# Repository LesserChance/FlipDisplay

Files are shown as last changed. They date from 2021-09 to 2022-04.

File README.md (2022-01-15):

# Flip Display

https://user-images.githubusercontent.com/819400/149609962-681a9211-6ebb-46da-95a2-772721c91d99.mp4

This is a 3D-printed flip character display. Each character utilizes a position sensor for loop detection in order to ensure accuract positioning of character display. The display is capable of a few different animation styles, e.g. all arriving at the same time, or cascading left-to-right. It has a simple web-based UI and API, and is fairly easy to construct.

## UI
The ESP32 hosts a web server that serves a simple web page and API that allows you to update the display.

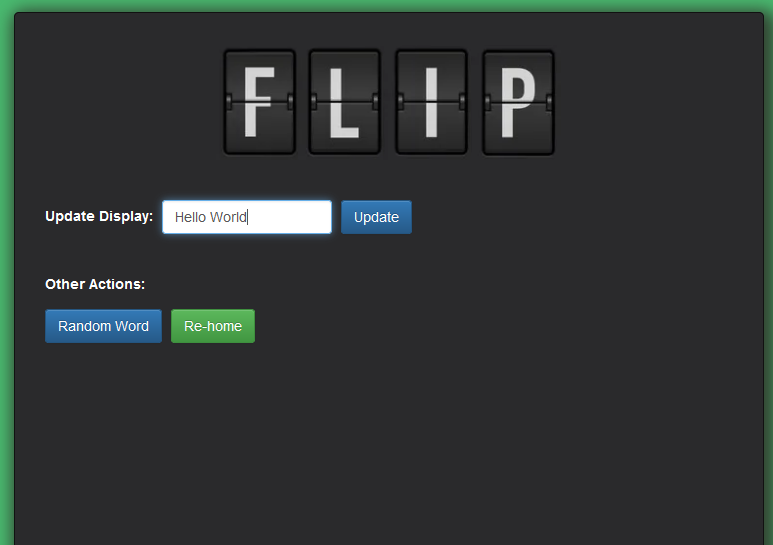
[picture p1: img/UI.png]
UI


## Electronics
There are only a few different major components: A buck convertor, an ESP32, and an A4988 Motor driver (per character)

### PCB: Main
The main panel is used as the power bus and ESP32 break out. It connects each motor step pin and loop detection button pin to an individual GPIO pin, and connects all driver enable pins to a single GPIO pin. There is also a section for screw terminals for easy access to all ESP32 pins, as well as power.

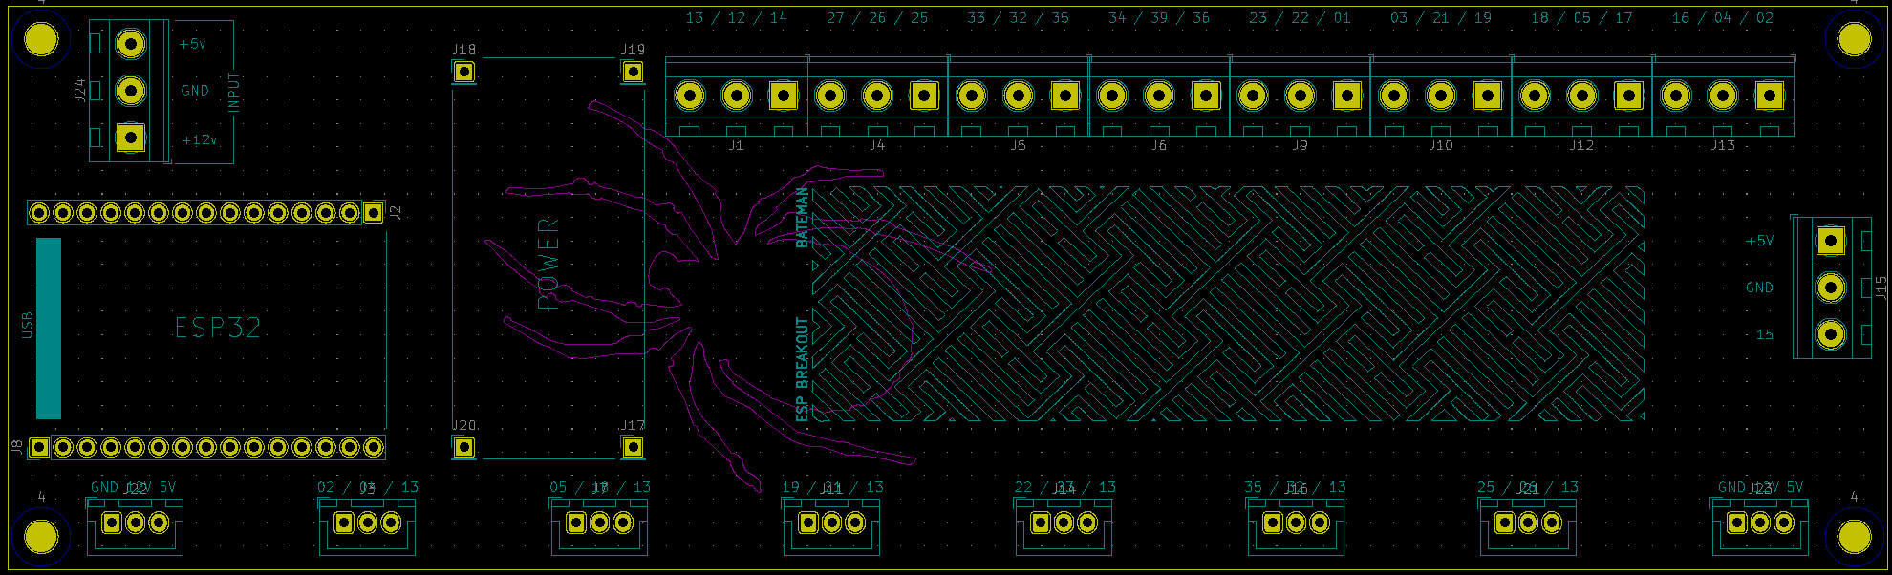
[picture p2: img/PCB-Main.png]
Main PCB


### PCB: Motor
One motor panel exists per character. This acts as the interface between the A4988 Motor Driver, the motor, and the ESP32.

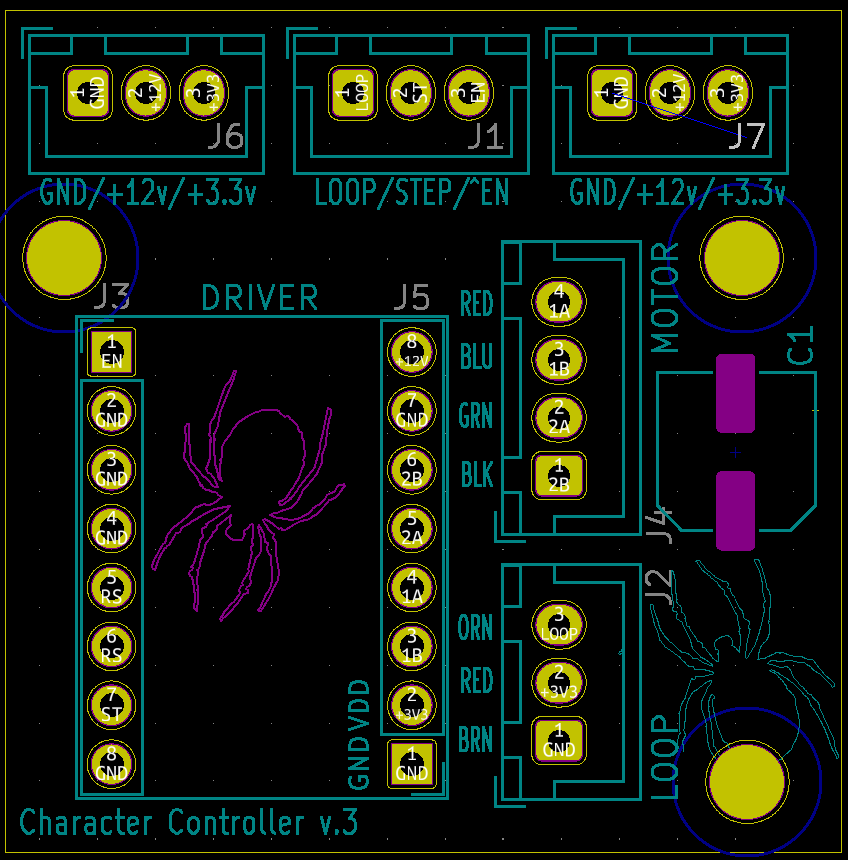
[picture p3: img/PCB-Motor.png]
Motor PCB


## Models
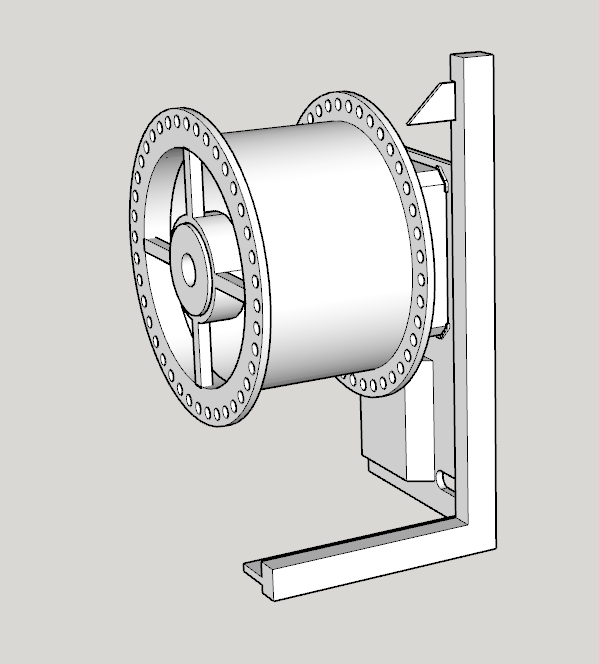
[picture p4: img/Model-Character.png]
models


The character models are designed to be nested against one another and to minimize the distance between characters as much as possible.

### Assembly 1: The Barrel
The barrel and the stator connect to one another, and the flaps are placed within the holes.

### Assembly 2: The Bracket
A motor is mounted to the bracket. The button holder is connected to the two front bottom holes on the motor and a leaf switch button is glued on. The barrel assembly is connected to the motor with a coupler so that it rotates around the motor housing. A stopper is fastened into the top of the bracket, which is used to stop the letters at a certain position

### Assembly 3: Circuit
The circuit assembly is just used to house the individual PCBs.

---

Originally inspired from designs by [hakernia on Thingiverse](https://www.thingiverse.com/thing:2369832), but I found that the small motor was not driving well, as it'd get hot and fail, or get stuck easily. So I upgraded to heavier duty Nema17 Motorslike the ones used in 3D Printers and decided to use an actual coupler to connect the 3d printed parts to the motor.

## Supplies and Costs
A 6 character Flip Display will cost about $170.00 USD for all the raw materials, then additional costs based on your enclosure.  

Filament: $40.00 USD  
Electronics: $100.00 USD  
PCBs: $30.00 USD  

### Bill of Materials
All models were printed using [MatterHackers Build Series PLA](https://www.matterhackers.com/store/l/175mm-pla-filament-black-1-kg/sk/MY6CYEZM) on a Creality 10s Pro V2.
| Part | Supply | Cost | Count |
|---|---|---|---|
|Black PLA|[MatterHackers](https://www.matterhackers.com/store/l/175mm-pla-filament-black-1-kg/sk/MY6CYEZM)|$19.00|1|
|White PLA|[MatterHackers](https://www.matterhackers.com/store/l/175mm-pla-filament-white-1-kg/sk/MEEDKTKU)|$19.00|1|

Electronics and hardware were sourced through a few different providers.

| Component | Part | Supply | Cost | Count |
|---|---|---|---|---|
|-|12v Power adaptor|[Amazon](https://www.amazon.com/gp/product/B07FFKL7CR/ref=ppx_yo_dt_b_asin_title_o05_s00)|$19.00|1|
|Main|Buck Convertor|[Amazon](https://www.amazon.com/gp/product/B07QKHR6PY/ref=ppx_yo_dt_b_asin_title_o05_s00)|$1.50|1|
|Main|ESP32|[Amazon](https://www.amazon.com/gp/product/B08246MCL5/ref=ppx_yo_dt_b_asin_title_o04_s00)|$7.00|1|
|Main|Panel Mount Micro USB Extension|[Amazon](https://www.amazon.com/gp/product/B082HZKVP1/ref=ppx_yo_dt_b_asin_title_o05_s01)|$11.00|1 (optional)|
|Main|15 Pin Header|[Tayda](https://www.taydaelectronics.com/15-pin-2-54-mm-single-row-female-pin-header.html)|$0.12|2|
|Main|Screw Terminal|[Tayda](https://www.taydaelectronics.com/dg300-screw-terminal-block-3-positions-5mm.html)|$0.14|A bunch|
|Motor|Nema17 Stepper Motor|[Amazon](https://www.amazon.com/gp/product/B07THK8RS1/ref=ppx_yo_dt_b_asin_title_o01_s00)|$7.40|1 per character|
|Motor|A4988 Motor Driver|[Amazon](https://www.amazon.com/gp/product/B092PZNFNS/ref=ppx_yo_dt_b_asin_title_o05_s00)|$1.40|1 per character|
|Motor|Coupler|[Amazon](https://www.amazon.com/gp/product/B0852P8WSH/ref=ppx_yo_dt_b_asin_title_o09_s00)|$0.90|1 per character|
|Motor|10mm x 26mm x8mm Bearing|[Digikey](https://www.digikey.com/en/products/detail/mechatronics-bearing-group/6000-2RS/9608370)|$0.85|1 per character|
|Motor|Leaf Switch|[Mouser](https://www.mouser.com/ProductDetail/612-MS0850506F020V2A)|$1.33|1 per character|
|Both|DC Power Jack|[Tayda](https://www.taydaelectronics.com/dc-power-jack-2-1mm-enclosed-frame-with-switch.html)|$0.13|1|
|Both|8 Pin Header|[Tayda](https://www.taydaelectronics.com/8-pin-2-54-mm-single-row-female-pin-header.html)|$0.08|A bunch|
|Both|2 Pin JST Connector|[Tayda](https://www.taydaelectronics.com/2-pins-jst-xh-2-54-male-connector-straight-180-degree.html)|$0.01|A bunch|
|Both|3 Pin JST Connector|[Tayda](https://www.taydaelectronics.com/3-pins-jst-xh-2-54-male-connector-straight-180-degree.html)|$0.02|A bunch|
|Both|5 Pin JST Connector|[Tayda](https://www.taydaelectronics.com/5-pins-jst-xh-2-54-male-connector-straight-180-degree.html)|$0.03|A bunch|

All PCBs were printed using [JLCPCB](https://jlcpcb.com/).  
| Part | Supply | Cost | Count |
|---|---|---|---|
|Main PCB|[JLCPCB](https://jlcpcb.com/) (requires SMT assembly)|$9.00|1|
|Motor PCB|[JLCPCB](https://jlcpcb.com/)|$1.70|1 per character|

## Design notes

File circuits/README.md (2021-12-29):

# Flip Display Circuits
Circuits were designed using KiCad. You should be able to pull the zip files out of the gerber directories for each schematic and upload that into JLCPCB. In the case of the motor PCB, you'll also need to upload the BOM and CPL files for SMT assembly.

## Main PCB
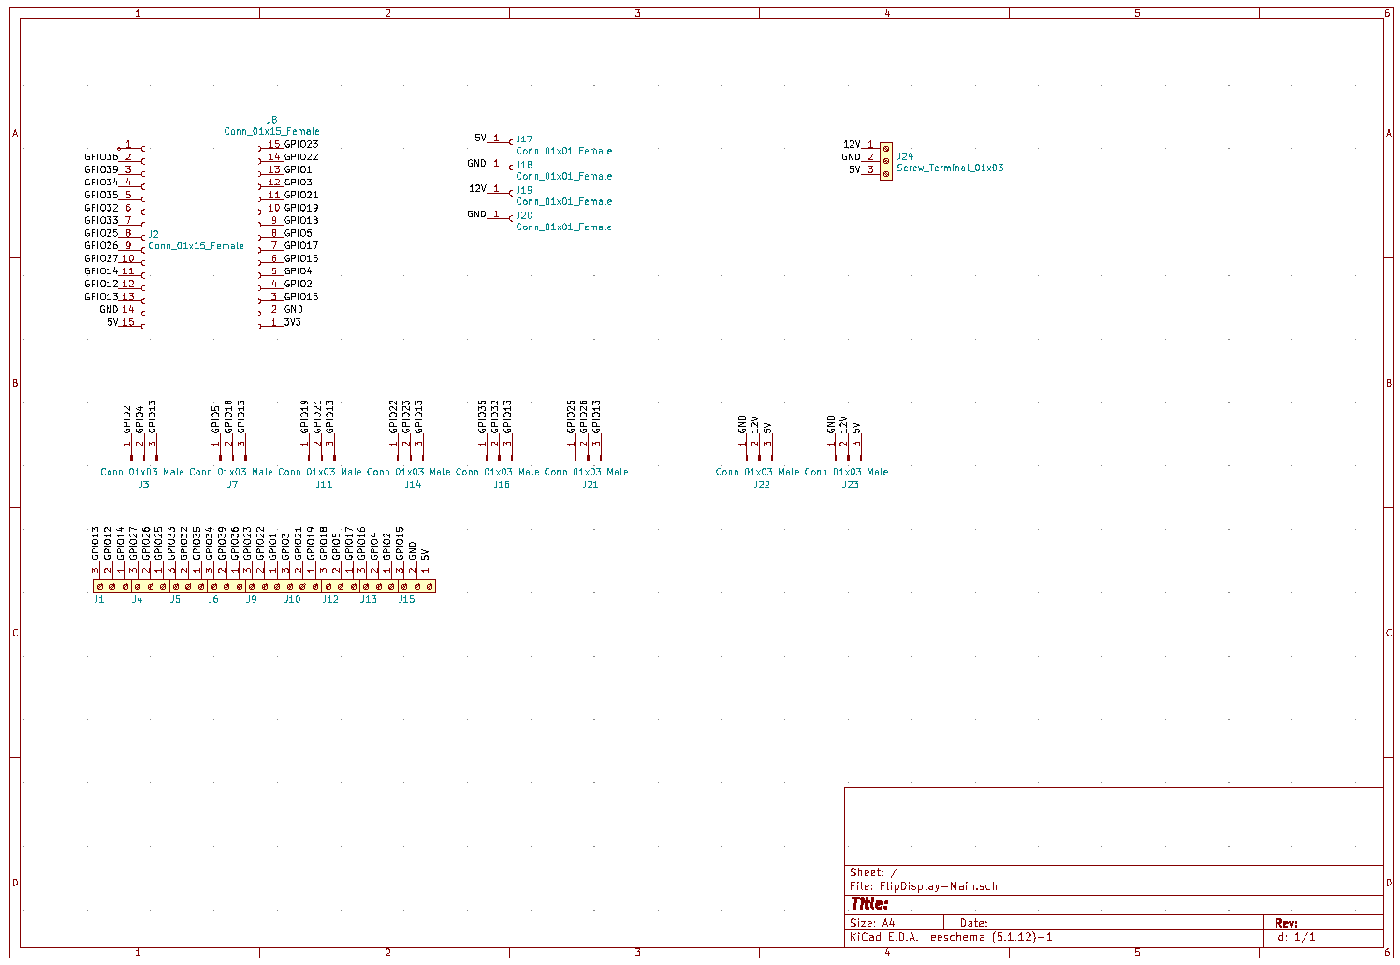
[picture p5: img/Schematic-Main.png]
Main PCB


## Motor PCB
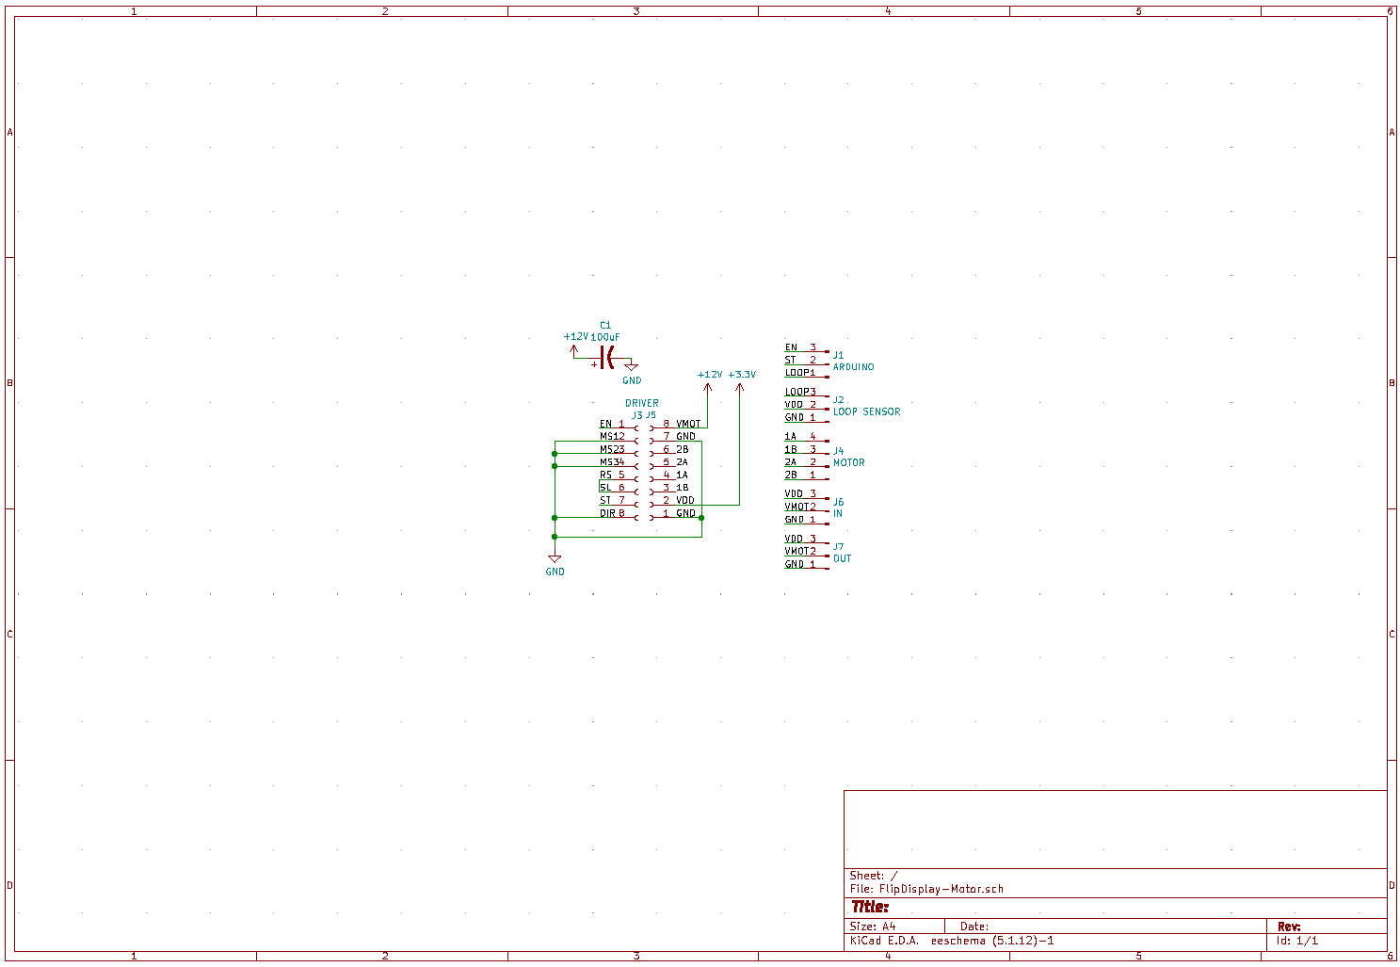
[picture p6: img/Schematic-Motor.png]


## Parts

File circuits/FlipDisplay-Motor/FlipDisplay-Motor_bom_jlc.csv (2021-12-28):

Comment | Designator | Footprint | LCSC Part #
100uF | C1 | C_Elec_6.3x7.7 | C2836443

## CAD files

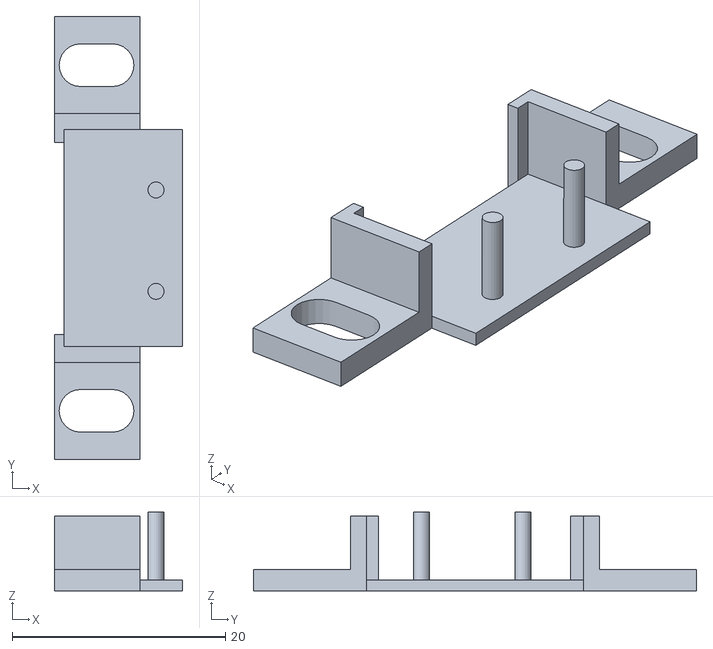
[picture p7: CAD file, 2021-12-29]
models/Button.stl
12.0 x 41.5 x 7.39

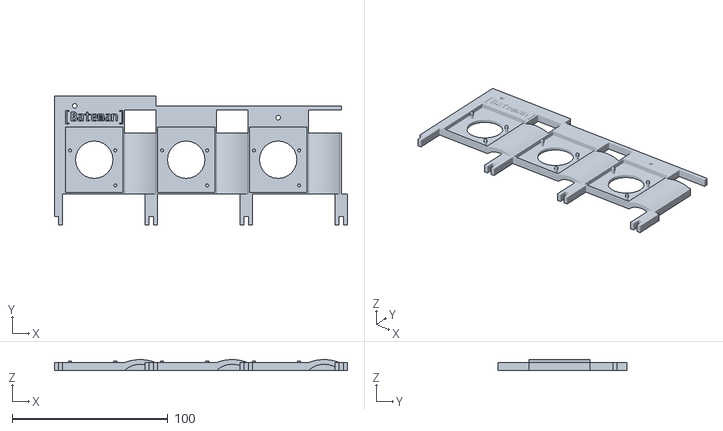
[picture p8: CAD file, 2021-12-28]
models/Circuit-Left.stl
188.0 x 83.0 x 7.00

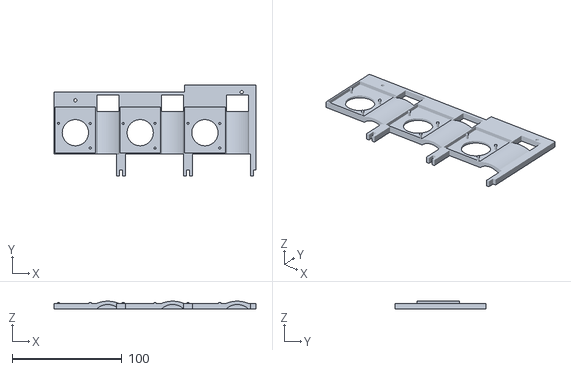
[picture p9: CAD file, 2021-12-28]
models/Circuit-Right.stl
184.0 x 83.0 x 7.00

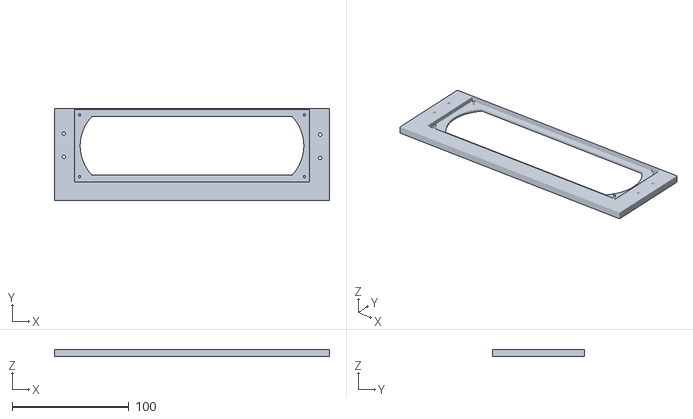
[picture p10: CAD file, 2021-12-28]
models/Circuit-Back.stl
236.0 x 79.0 x 6.00

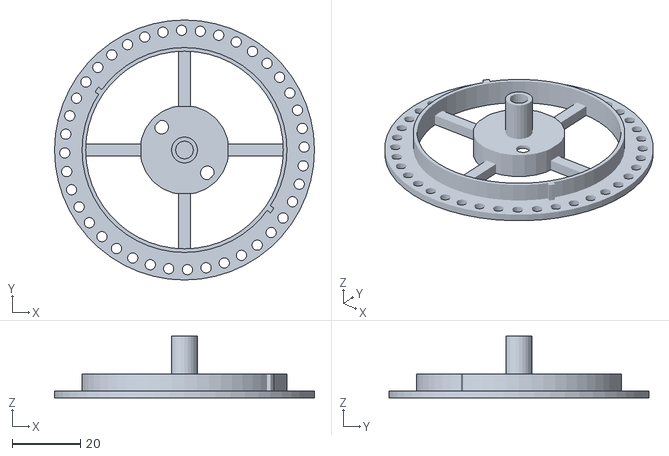
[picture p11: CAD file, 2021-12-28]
models/Stator.stl
76.0 x 76.0 x 18.0

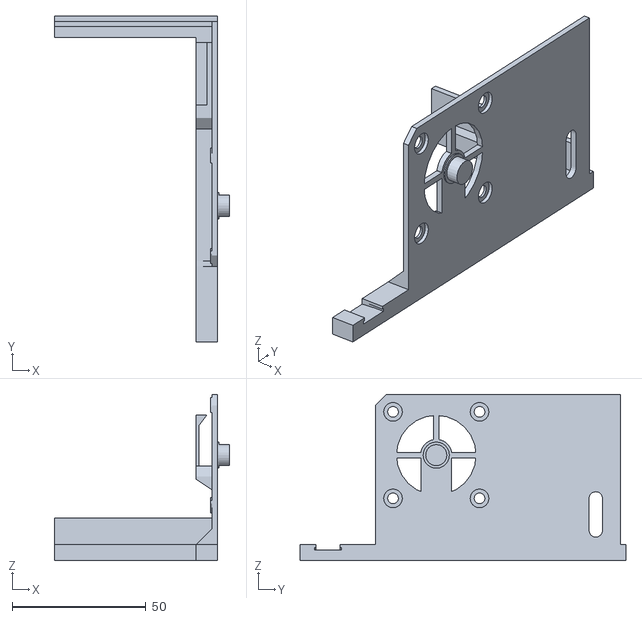
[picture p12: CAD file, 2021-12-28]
models/Bracket.stl
65.5 x 122.0 x 62.3

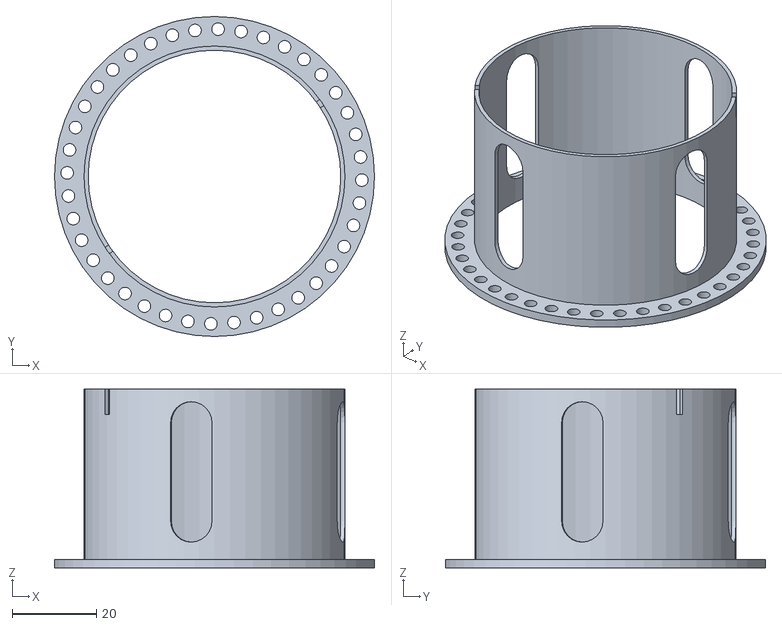
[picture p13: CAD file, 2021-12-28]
models/Barrel.stl
76.0 x 76.0 x 42.5

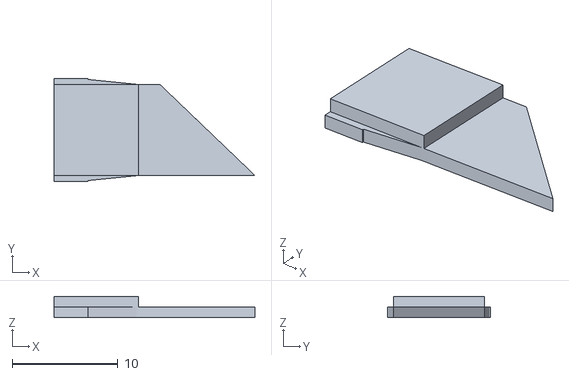
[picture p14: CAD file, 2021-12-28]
models/Stopper.stl
19.0 x 9.76 x 2.00

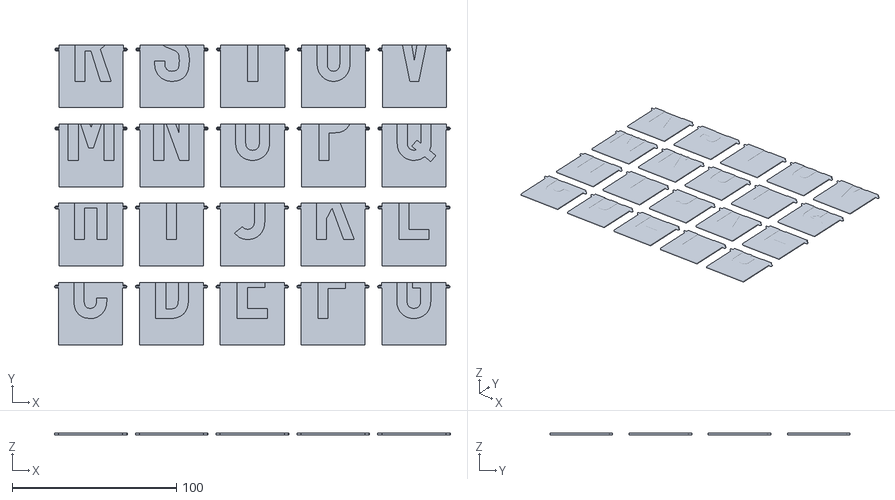
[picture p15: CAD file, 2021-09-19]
models/Flaps-CV.stl
240.9 x 182.4 x 1.20

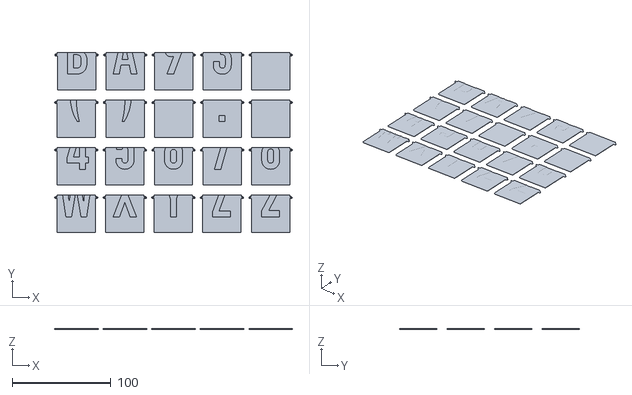
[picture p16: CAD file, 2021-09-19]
models/Flaps-WB.stl
240.8 x 182.4 x 1.20

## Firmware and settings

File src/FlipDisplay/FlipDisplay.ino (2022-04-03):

#include "FlipDisplay.h"
#include "FlipDisplayServer.h"
#include "ProgramClock.h"
#include "ProgramSonos.h"

FlipDisplay display;
FlipDisplayServer server;
ProgramClock progClock;
ProgramSonos progSonos;

bool buttonOneTriggered = false;
bool buttonTwoTriggered = false;
uint8_t buttonOneLastState;
uint8_t buttonTwoLastState;
unsigned long buttonOneDebounceStart = 0;
unsigned long buttonTwoDebounceStart = 0;

uint8_t currentProgram = 0;

void initializeGPIO() {
    Serial.begin(115200);
    Serial.println("START");

    pinMode(enablePin, OUTPUT);

    for (int i = START_CHARACTER; i < CHARACTER_COUNT; i++) {
        pinMode(STEP_PIN[i], OUTPUT);
        pinMode(LOOP_PIN[i], INPUT);
        digitalWrite(STEP_PIN[i], LOW);
    }

    pinMode(TEST_PIN_ONE, INPUT_PULLUP);
    pinMode(TEST_PIN_TWO, INPUT_PULLUP);
    
    buttonOneLastState = digitalRead(TEST_PIN_ONE);
    buttonTwoLastState = digitalRead(TEST_PIN_TWO);
}

void initializePrograms() {
    progClock = ProgramClock(&display);
    progClock.setupProgram();

    progSonos = ProgramSonos(&display);
    progSonos.setupProgram();
}

void setup() {
    initializeGPIO();

    display = FlipDisplay();
    display.setupDisplay();

    server = FlipDisplayServer(&display);
    server.setupServer();
    
    initializePrograms();
}

unsigned long lastTime = 0;

void readButtons() {
    if (buttonOneTriggered) {
        Serial.println("BUTTON ONE");
        buttonOneTriggered = false;
    }

    if (buttonTwoTriggered) {
        Serial.println("BUTTON TWO");
        buttonTwoTriggered = false;
    }

    uint8_t buttonOneState = digitalRead(TEST_PIN_ONE);
    uint8_t buttonTwoState = digitalRead(TEST_PIN_TWO);
    unsigned long currentTime = millis();

    if (buttonOneDebounceStart == 0 && buttonOneState != buttonOneLastState) {
        buttonOneDebounceStart = currentTime;
    }
    if (buttonOneDebounceStart != 0 && buttonOneDebounceStart + 100 < currentTime) {
        buttonOneTriggered = true;
        buttonOneDebounceStart = 0;
        buttonOneLastState = buttonOneState;
    }

    if (buttonTwoDebounceStart == 0 && buttonTwoState != buttonTwoLastState) {
        buttonTwoDebounceStart = currentTime;
    }
    if (buttonTwoDebounceStart != 0 && buttonTwoDebounceStart + 100 < currentTime) {
        buttonTwoTriggered = true;
        buttonTwoDebounceStart = 0;
        buttonTwoLastState = buttonTwoState;
    }
}

void loop() {
    readButtons();

    if (buttonTwoTriggered) {
        currentProgram = (currentProgram + 1) % 3;
        switch (currentProgram) {
            case 0:
                display._programName = "Clock";
                Serial.println("PROGRAM: CLOCK");
                break;
            case 1:
                display._programName = "Sonos";
                Serial.println("PROGRAM: SONOS");
                break;
            case 2:
                display._programName = "None";
                Serial.println("PROGRAM: NONE");
                break;
        }
    }

    switch (currentProgram) {
        case 0:
            progClock.run(buttonOneTriggered, buttonTwoTriggered);
            break;
        case 1:
            progSonos.run(buttonOneTriggered, buttonTwoTriggered);
            break;
        case 2:
            // no program
            if (buttonOneTriggered) {
                String word = words[random(0, WORD_COUNT)];
                display.setDisplay(word, MICROSECONDS * 30, true);
            }
            break;
    }

    display.run();
}

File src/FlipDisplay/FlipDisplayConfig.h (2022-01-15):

#ifndef FlipDisplayConfig_H
#define FlipDisplayConfig_H

#include <Arduino.h>
#include <SPIFFS.h>

#include "Secrets.h"

#define DEBUG 1
#define DEBUG_LOOP 0
#define DEBUG_LERP 0
#define DEBUG_RESPONSES 1

#define WIFI_FAIL_COUNT 20

#define loopPin1 2
#define loopPin2 5
#define loopPin3 19
#define loopPin4 22
#define loopPin5 35
#define loopPin6 25

#define stepPin1 4
#define stepPin2 18
#define stepPin3 21
#define stepPin4 23
#define stepPin5 32
#define stepPin6 26

#define enablePin 13

#define TEST_PIN_ONE 15                    // manual trigger (yellow)
#define TEST_PIN_TWO 16                    // manual trigger (green)

#define TOTAL_CHARACTERS 6                 // the total number of characters we're able to control
#define START_CHARACTER 0                  // which index is the first character (allows you to test just characters at the end)
#define CHARACTER_COUNT 6                  // how many characters will the animations actually control (out of total)
#define MAX_WORD_COUNT 30                  // the maximum number of words that a display cna be chunked into

#define MIN_STEP_DURATION 2000             // time between steps when moving as fast as possible
#define AVG_STEP_DURATION 4600             // time between steps for an average running speed
#define HOMING_STEP_DURATION 6000          // time between steps when homing

#define LOOP_REVERSE_OFFSET 1              // for a loop detected while running, this offset adjusts for the fact that its moving fast and oversteps

#define MICROSECONDS 1000000
#define DEBOUNCE_DURATION 50000            // how long to wait (microseconds) to debounce the loop button
#define STEPS_PER_REVOLUTION 400           // total numbers of steps to make a full rotation
#define POSSIBLE_CHARACTER_VALUES 40       // total number of characters that can be displayed
#define STEPS_PER_CHARACTER 10             // how many steps to step a single character
#define MIN_STEPS_PER_LERP 200             // if a lerp is below this number of steps, itll do a full loop
#define PAUSE_ENABLED_DURATION (MICROSECONDS * 5) // how long to wait (microseconds) before disabling the motor entirely when paused

#define SCROLLING_ENABLED 1                // should the display scroll for strings that are too large?
#define WAIT_TO_SCROLL (MICROSECONDS * 1)    // how long should we pause until we scroll to the next set of characters
#define CHARS_TO_SCROLL 3                  // how many characters should scroll at a time

const int STEP_PIN[TOTAL_CHARACTERS] = {stepPin1, stepPin2, stepPin3, stepPin4, stepPin5, stepPin6};
const int LOOP_PIN[TOTAL_CHARACTERS] = {loopPin1, loopPin2, loopPin3, loopPin4, loopPin5, loopPin6};
const int CHARACTER_OFFSET[TOTAL_CHARACTERS] = {24,48,37,39,323,34};

#define WIFI_SSID_PATH "/ssid.txt"
#define WIFI_PASSWORD_PATH "/pass.txt"
#define SONOS_ACCESS_TOKEN_PATH "/sonos_access_token.txt"
#define SONOS_RESET_TOKEN_PATH "/sonos_reset_token.txt"
#define SONOS_GROUP_ID_PATH "/sonos_group_id.txt"

class FlipDisplayConfig {
   public:
    typedef enum {
        WIFI_SSID = 0,
        WIFI_PASSWORD = 1,
        SONOS_ACCESS_TOKEN = 2,
        SONOS_GROUP_ID = 3,
        SONOS_RESET_TOKEN = 4
    } ConfigKey;

    static void initializePersistedValues();
    static String getPersistedValue(ConfigKey key);
    static void setPersistedValue(ConfigKey key, const char * message);
    static void deletePersistedValue(ConfigKey key);
    
   private:
    static void initSPIFFS();

    static String readFile(fs::FS &fs, const char * path);
    static void writeFile(fs::FS &fs, const char * path, const char * message);
    static void deleteFile(fs::FS &fs, const char * path);
};

#endif

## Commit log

2021-09-19 Initial commit
    Adding firmware, schematic image
2021-09-19 Add Models
    Update readme
    [Barrel.stl, Face.stl, Flaps-final-CV.stl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]
2021-10-16 Code update
    button press now displays a random word from a list. better loop detection. better handle multiple boards and motors per board.
2021-11-05 Reset parallelization, set clock when not in use
    [FlipDisplay.ino]
2021-12-28 Full Stepping, Disable motors when not in use
2021-12-28 Add new models and finalized circuits
    [Barrel.stl, Bracket.stl, Circuit-Back.stl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]
2021-12-29 README updates
    [Button.stl]
2021-12-29 circuit readme
2022-01-03 Add Sonos Currently Playing
2022-01-04 add reset token. do some cleanup, fix buttons
    [FlipDisplay.cpp, FlipDisplay.h, FlipDisplay.ino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]
2022-01-14 power toggle, display duration, program switcher
